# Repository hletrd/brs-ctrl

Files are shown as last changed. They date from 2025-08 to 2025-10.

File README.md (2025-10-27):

# BEHAVIOR Robot Suite: Streamlining Real-World Whole-Body Manipulation for Everyday Household Activities

## This repository is a fork of the original [BEHAVIOR Robot Suite](https://github.com/behavior-robot-suite/brs-ctrl) repository.

* A 3D printer–friendly version of the JoyLo arms, featuring optimized 3D models for improved printability and easier assembly.

### Changes

* Merged `jcC.obj` and `jcSpace_33mm.obj` into a single `jcC.obj`.
* Adjusted the M2 nut pocket in `jcA.obj` to be tighter to ensure the fit of the nut.
* Added a slight draft and chamfer to the bottom of `jcB.obj` to make the holder easier to insert.
* Reduced the height to 2.0mm from the motor insertion area in `l2.obj`, `l2back.obj`, `l4.obj`, `l5.obj`, and `jcC.obj` so that the motor can be freely moved without the parts touching each other.
* Fixed mesh issues in `l3.obj`.
* Added an alignment key to `l2.obj` and `l2back.obj` to ensure precise alignment during assembly.
* Reduced the face thickness of `l4.obj` from motor mounting side to prevent interference with `l5.obj`.
* Rotated all parts so they can be printed with the fewest possible supports.

#### Note

* The final dimensions of the JoyLo arms remain unchanged, except for the wrist hinge (if a spacer is inserted).
* If exact dimensions are critical, **do not insert the spacer**.
  * Note that the wrist hinge might damage the cable.

### Printing instructions

* Print all parts, one set per arm.
  * Mirror `jcA.obj` and `jcC.obj` for the right side.

#### Recommended printing parameters

* Material: PLA
* Layer height: 0.2mm
* Outer wall thickness: 0.8mm
* Infill density: 50%
* Infill pattern: Grid or Gyroid
* Supports: Required.
* Do not rotate. Just print as provided.
* Units are in millimeters.

#### Recommended printer setup

* Tested with Bambu X1 Carbon (0.4mm hardened steel nozzle) using BambuStudio as the slicer.
* Filament: Bambu PLA Basic.
* Default 0.20mm Standard profile with the following modifications:
  * Ironing Type: Top surfaces
  * Bottom shell layers: 5
  * Sparse infill density: 50%
  * Sparse infill pattern: Gyroid
  * Enable Support: Yes

### Assembly instructions

* Follow the [Assembly Guide](https://behavior-robot-suite.github.io/docs/sections/joylo/step_by_step_assembly_guidance.html) from the original repository.
* BOM are as following table. (for both arms)

#### 3D Printed Parts

| Part | Source | Description | Count | Notes |
|---|---|---|---|---|
| [`mount.obj`](hardware/joylo/mount.obj) | 3D Print | Part from the original repository. | 2 | |
| [`mountback.obj`](hardware/joylo/mountback.obj) | 3D Print | Part from the original repository. | 2 | |
| [`jcA.obj`](hardware/joylo/jcA.obj) | 3D Print | Part from the original repository. | 1 | |
| `jcA.obj` (Mirrored) | 3D Print | Mirror for the right side. | 1 | |
| [`jcB.obj`](hardware/joylo/jcB.obj) | 3D Print | Part from the original repository. | 2 | |
| [`jcC.obj`](hardware/joylo/jcC.obj) | 3D Print | Part from the original repository. | 1 | |
| `jcC.obj` (Mirrored) | 3D Print | Mirror for the right side. | 1 | |
| [`l2.obj`](hardware/joylo/l2.obj) | 3D Print | Part from the original repository. | 2 | |
| [`l2back.obj`](hardware/joylo/l2back.obj) | 3D Print | Part from the original repository. | 2 | |
| [`l3.obj`](hardware/joylo/l3.obj) | 3D Print | Part from the original repository. | 2 | |
| [`l4.obj`](hardware/joylo/l4.obj) | 3D Print | Part from the original repository. | 2 | |
| [`l5.obj`](hardware/joylo/l5.obj) | 3D Print | Part from the original repository. | 2 | |
| [`u2d2_mount.obj`](hardware/joylo/u2d2_mount.obj)| 3D Print | Part from the original repository. | 1 | |
| [`spacer.obj`](hardware/joylo/spacer.obj) |3D Print| Optional spacer for the wrist hinge. | 2 | If the wrist hinge is too tight, insert this spacer for easier assembly. |

#### Miscellaneous Parts

| Part | Description | Count | Notes |
|---|---|---|---|
| M2 x 12mm bolts | For securing `jcA.obj` to `jcC.obj`. | 4 | |
| M2 nuts | Used with M2 x 12mm bolts to secure `jcA.obj` to `jcC.obj`. | 4 | |
| M2 x 8mm screws | For mounting all motors on their housings. | 24 | |
| M2 x 6mm bolts | For mounting all motors onto rotational axes. | 64 | |
| M2 x 10mm screws | For mounting motors to the wrist hinge. | 4 | |
| M3 x 6mm nylon support (M) | For mounting the u2d2 board. | 4 | |
| M3 nuts | Used with M3 x 6mm nylon support (M) to mount the u2d2 board. | 4 | |

* Note the difference of bolts and screws.

---

<div align="center">

[Yunfan Jiang](https://yunfanj.com/),
[Ruohan Zhang](https://ai.stanford.edu/~zharu/),
[Josiah Wong](https://jdw.ong/),
[Chen Wang](https://www.chenwangjeremy.net/),
[Yanjie Ze](https://yanjieze.com/),
[Hang Yin](https://hang-yin.github.io/),
[Cem Gokmen](https://www.cemgokmen.com/),
[Shuran Song](https://shurans.github.io/),
[Jiajun Wu](https://jiajunwu.com/),
[Li Fei-Fei](https://profiles.stanford.edu/fei-fei-li)



**Conference on Robot Learning (CoRL) 2025**

[[Website]](https://behavior-robot-suite.github.io/)
[[arXiv]](https://arxiv.org/abs/2503.05652)
[[PDF]](https://behavior-robot-suite.github.io/assets/pdf/brs_paper.pdf)
[[Doc]](https://behavior-robot-suite.github.io/docs/)
[[Algorithm Code]](https://github.com/behavior-robot-suite/brs-algo)
[[Assembly Guide]](https://behavior-robot-suite.github.io/docs/sections/joylo/step_by_step_assembly_guidance.html)


[](https://behavior-robot-suite.github.io/docs/)



______________________________________________________________________
</div>

We introduce the **BEHAVIOR Robot Suite** (BRS), a comprehensive framework for learning whole-body manipulation to tackle diverse real-world household tasks. BRS addresses both hardware and learning challenges through two key innovations: **JoyLo** and [WB-VIMA](https://github.com/behavior-robot-suite/brs-algo).

JoyLo provides a general, cost-effective approach to whole-body teleoperation by integrating multifunctional joystick controllers mounted on the ends of two 3D-printed arms.  The mounting arms serve as scaled-down kinematic twins of the robot’s arms, enabling precise bilateral teleoperation. JoyLo also inherits key advantages of puppeteering devices, including intuitive operation, reduced singularities, and enhanced stability. By grasping the JoyCon controllers attached to the kinematic-twin arms, users can operate the arms, grippers, torso, and mobile base in unison. This significantly accelerates data collection by allowing users to perform bimanual coordination tasks, navigate safely and accurately, and guide the end-effectors to effectively reach various locations in 3D space.



## Getting Started

> [!TIP]
> 🚀 Check out the [doc](https://behavior-robot-suite.github.io/docs/sections/brs_ctrl/overview.html) for detailed installation and usage instructions!

To control the Galaxea R1 robot, simply do

```Python
from brs_ctrl.robot_interface import R1Interface
from brs_ctrl.robot_interface.grippers import GalaxeaR1Gripper

# Initialize the robot interface with grippers
robot = R1Interface(
    left_gripper=GalaxeaR1Gripper(
        left_or_right="left",
        gripper_close_stroke=0.0,
        gripper_open_stroke=100.0,
    ),
    right_gripper=GalaxeaR1Gripper(
        left_or_right="right",
        gripper_close_stroke=0.0,
        gripper_open_stroke=100.0,
    ),
)

# Control the robot
robot.control(
    arm_cmd={
        "left": left_arm_action,  # np (6,)
        "right": right_arm_action,  # np (6,)
    },
    gripper_cmd={
        "left": left_gripper_action,  # float between 0.0 and 1.0
        "right": right_gripper_action,  # float between 0.0 and 1.0
    },
    torso_cmd=torso_action,  # np (4,)
    base_cmd=mobile_base_action,  # np (3,)
)
```

To run real-robot JoyLo control, simply run

```bash
python3 scripts/joylo/real_joylo.py
```

To run data collection, simply run

```bash
python3 scripts/data_collection/start_data_collection.py
```

## Check out Our Paper
Our paper is posted on [arXiv](https://arxiv.org/abs/2503.05652). If you find our work useful, please consider citing us!

```bibtex
@inproceedings{
jiang2025brs,
title={{BEHAVIOR} Robot Suite: Streamlining Real-World Whole-Body Manipulation for Everyday Household Activities},
author={Yunfan Jiang and Ruohan Zhang and Josiah Wong and Chen Wang and Yanjie Ze and Hang Yin and Cem Gokmen and Shuran Song and Jiajun Wu and Li Fei-Fei},
booktitle={9th Annual Conference on Robot Learning},
year={2025},
url={https://openreview.net/forum?id=v2KevjWScT}
}
```

## License
This codebase is released under the [MIT License](LICENSE).

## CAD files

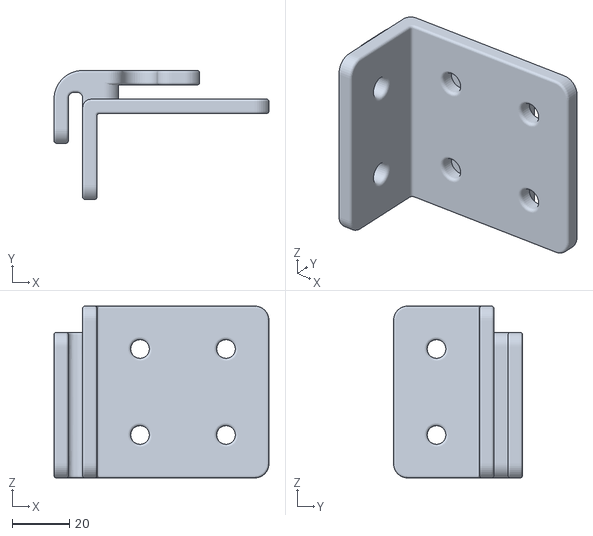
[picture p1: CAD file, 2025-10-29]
hardware/joylo/adapter.stl
75.0 x 45.0 x 60.0

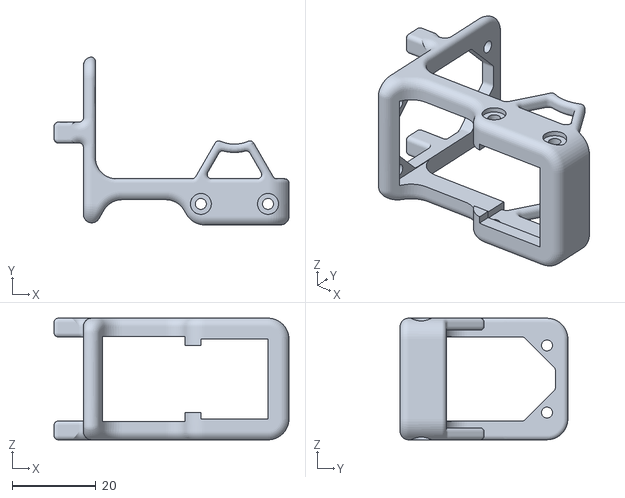
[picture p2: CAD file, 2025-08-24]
hardware/joylo_v2_7dof_arm/l7.obj
56.0 x 40.0 x 29.0

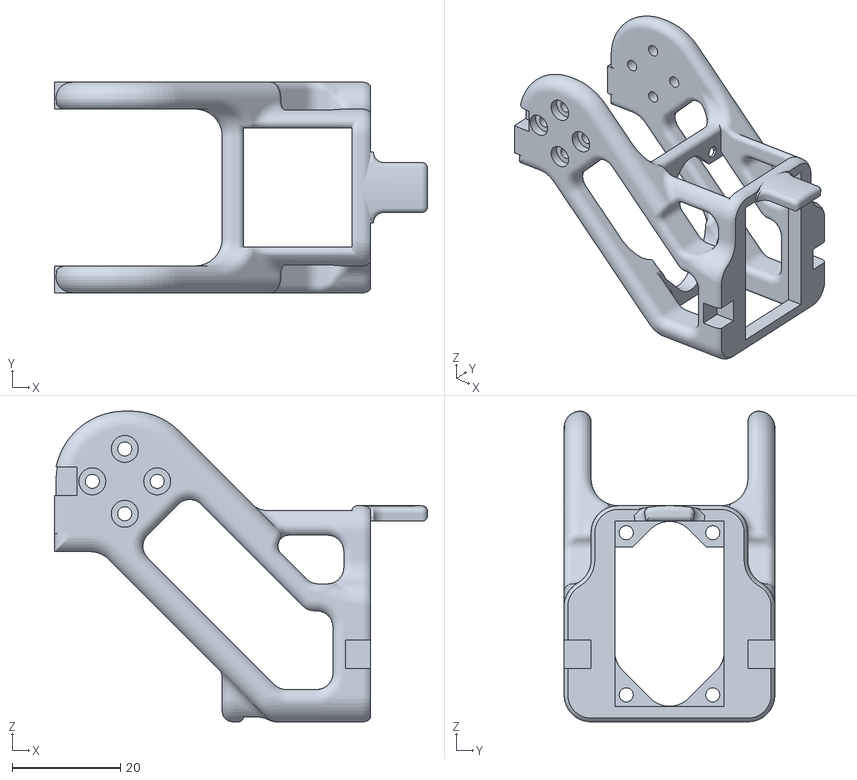
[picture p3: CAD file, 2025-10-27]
hardware/joylo/l4.stl
69.0 x 39.0 x 57.5

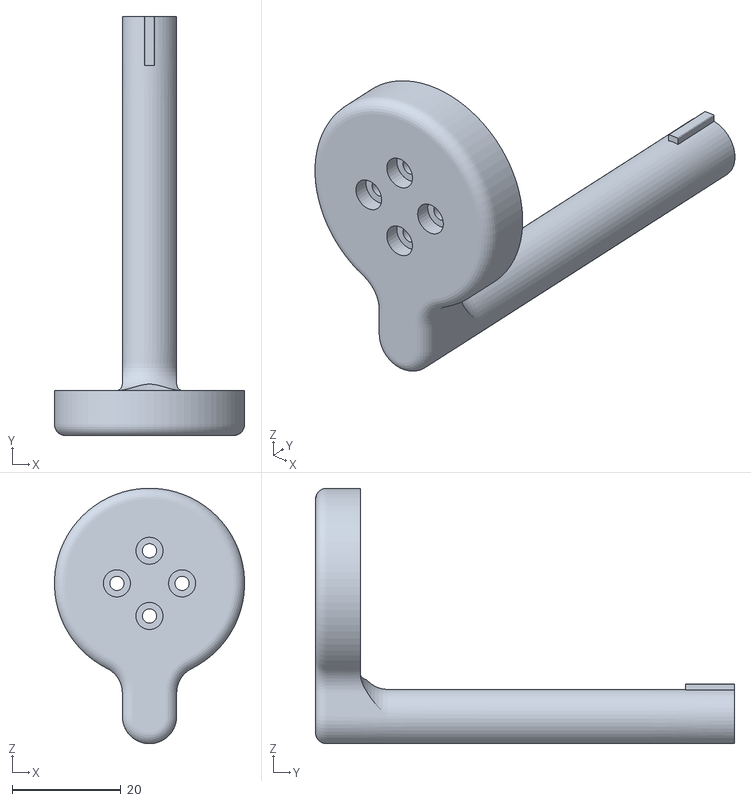
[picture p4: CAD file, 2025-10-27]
hardware/joylo/l2back.stl
35.0 x 77.1 x 47.0

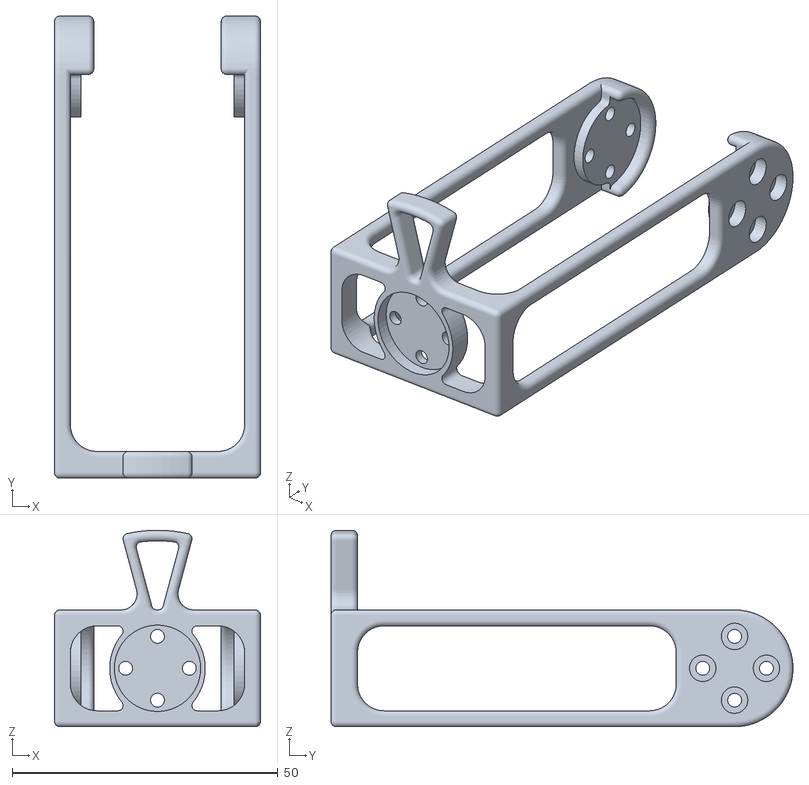
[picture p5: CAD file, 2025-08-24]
hardware/joylo_v2_7dof_arm/l6.obj
38.8 x 87.0 x 37.0

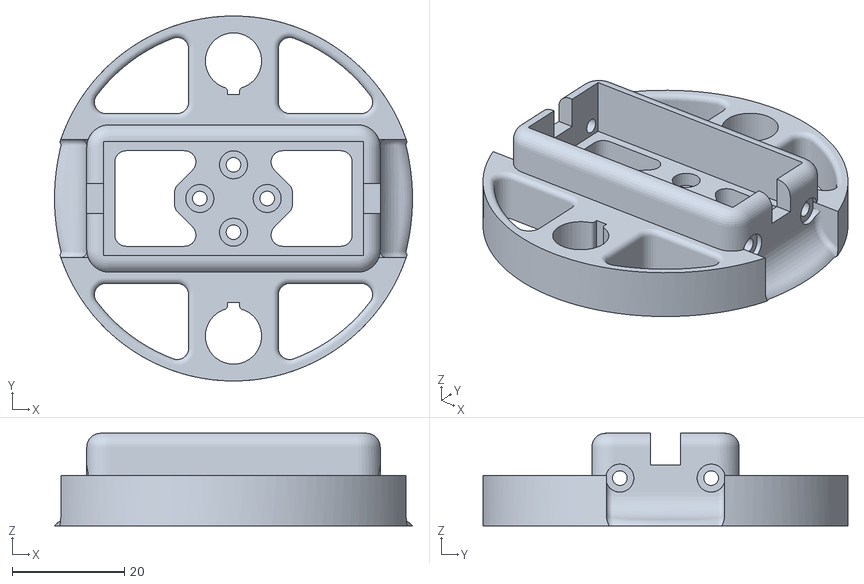
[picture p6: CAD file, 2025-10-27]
hardware/joylo/l2.stl
63.7 x 65.0 x 16.5

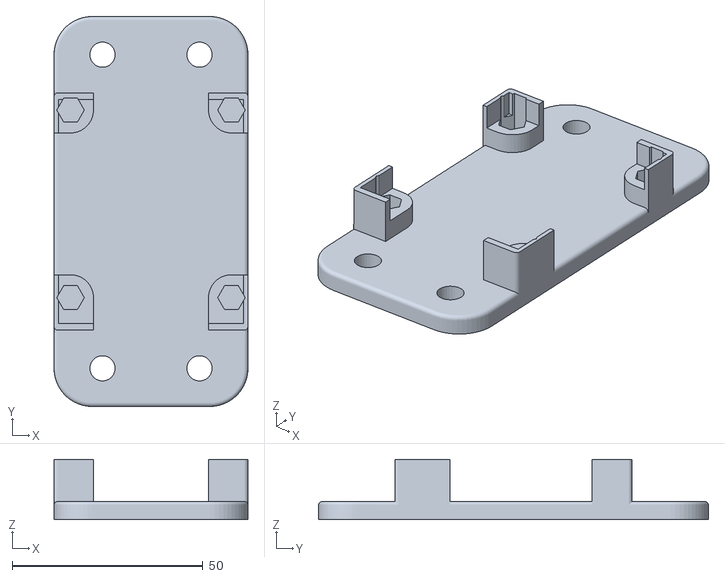
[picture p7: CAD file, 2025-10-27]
hardware/joylo/u2d2_mount.stl
50.8 x 102.1 x 15.8

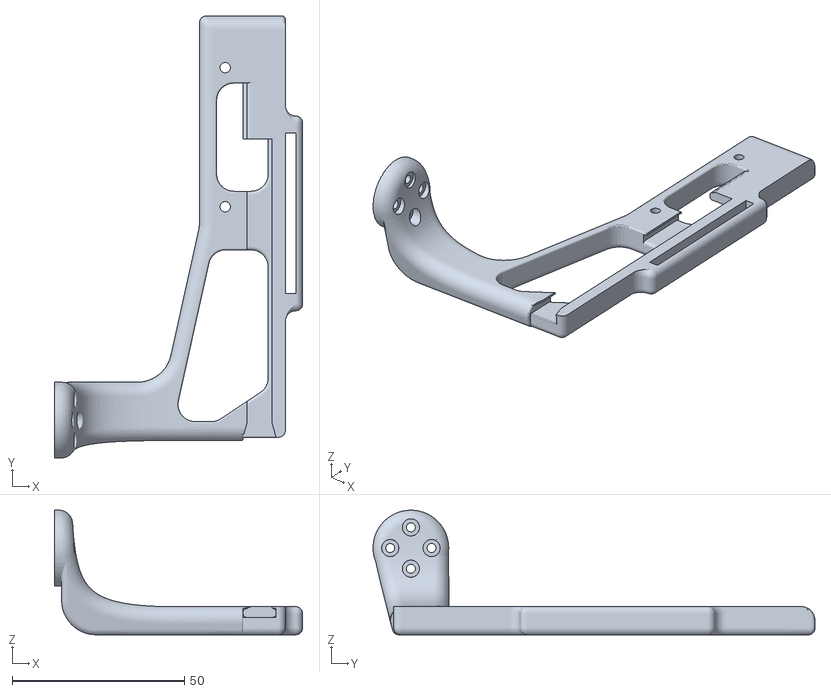
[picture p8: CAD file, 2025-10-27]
hardware/joylo/jcC.stl
72.1 x 128.3 x 36.2

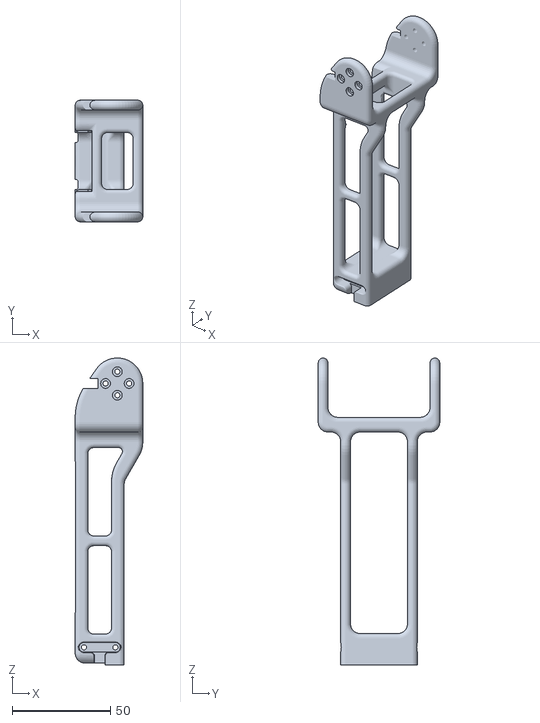
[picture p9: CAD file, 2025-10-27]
hardware/joylo/l3.stl
34.5 x 62.0 x 156.5

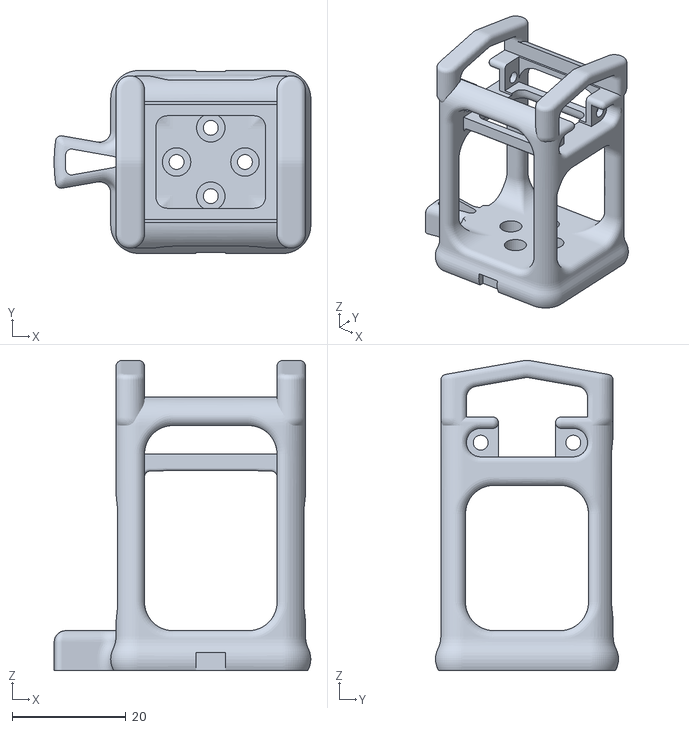
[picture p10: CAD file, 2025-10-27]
hardware/joylo/l5.stl
45.1 x 32.1 x 54.4

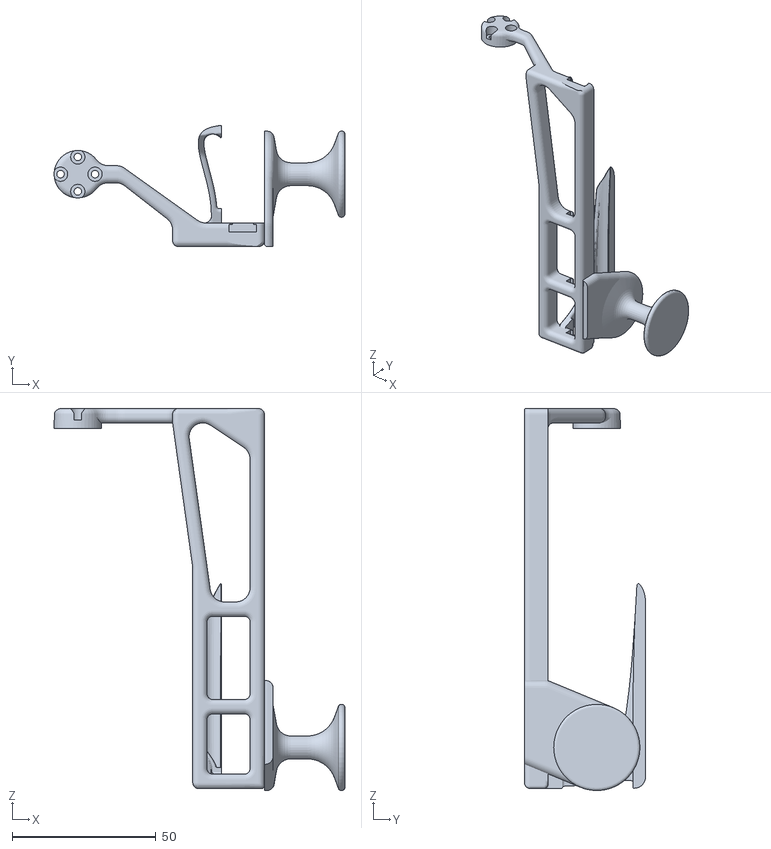
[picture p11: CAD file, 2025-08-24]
hardware/joylo_v2_7dof_arm/ljc.obj
101.2 x 42.2 x 133.0

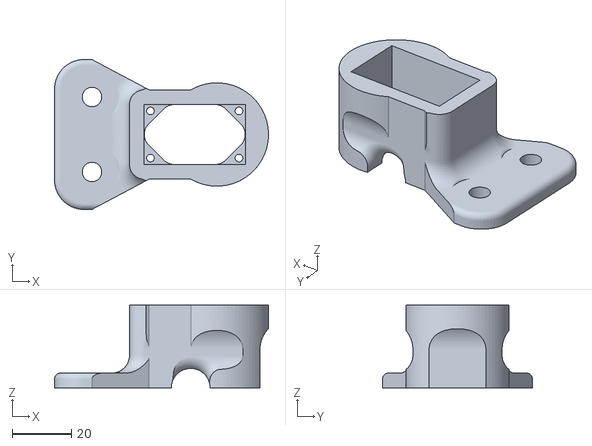
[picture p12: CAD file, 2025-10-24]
hardware/joylo/mount.stl
72.5 x 50.8 x 28.0

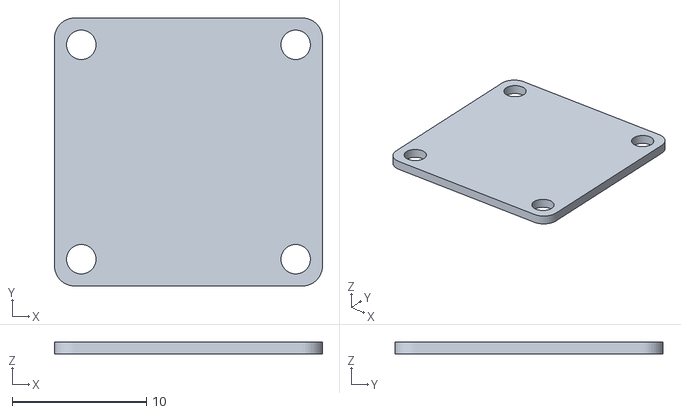
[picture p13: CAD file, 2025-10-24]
hardware/joylo/spacer.stl
20.0 x 20.0 x 0.9

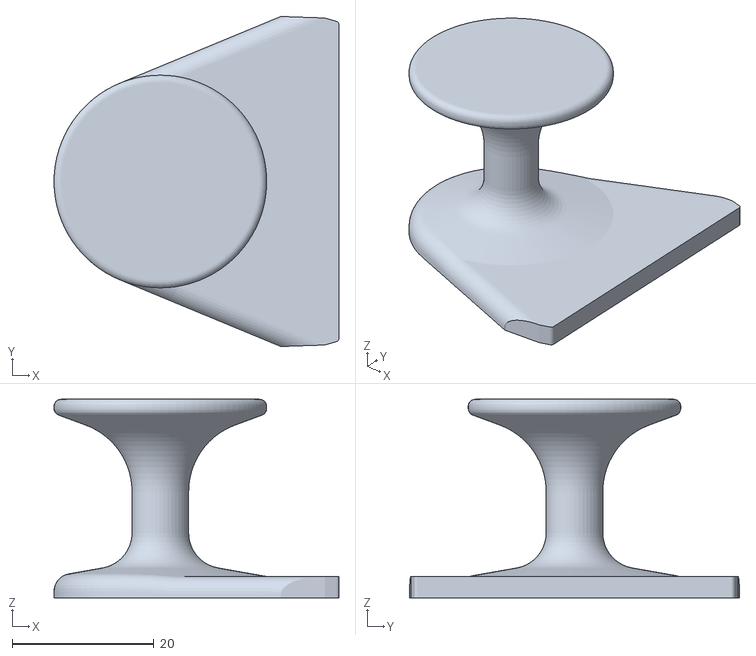
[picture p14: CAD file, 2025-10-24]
hardware/joylo/jcB.stl
40.2 x 46.6 x 28.0

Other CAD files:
hardware/joylo/jcA.stl
hardware/joylo/mountback.stl
hardware/joylo_v2_7dof_arm/l3.obj
hardware/joylo_v2_7dof_arm/l5.obj
hardware/joylo/adapter.obj
hardware/joylo/jcA.obj
hardware/joylo/jcB.obj
hardware/joylo/jcC.obj
hardware/joylo/l2.obj
hardware/joylo/l2back.obj
hardware/joylo/l3.obj
hardware/joylo/l4.obj
hardware/joylo/l5.obj
hardware/joylo/mount.obj
hardware/joylo/mountback.obj
hardware/joylo/spacer.obj
hardware/joylo/u2d2_mount.obj
hardware/joylo_v2_7dof_arm/l2.obj
hardware/joylo_v2_7dof_arm/l2back.obj
hardware/joylo_v2_7dof_arm/l4.obj
hardware/joylo_v2_7dof_arm/mount.obj
hardware/joylo_v2_7dof_arm/mountback.obj
hardware/joylo_v2_7dof_arm/u2d2_mount.obj

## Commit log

2025-08-24 add f3d files
    [jc.f3d, l2.f3d, l2back.f3d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]
2025-08-24 add 7dof joylo
    [l2.obj, l2back.obj, l3.obj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]
2025-10-24 updated mesh files
    [jcA.obj, jcA.stl, jcB.obj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]
2025-10-24 apply rotations
    [jcA.obj, jcA.stl, jcB.obj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]
2025-10-24 remove f3d files
    [jc.f3d, l2.f3d, l2back.f3d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]
2025-10-27 fix models
    [jcB.obj, jcC.obj, jcC.stl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]
2025-10-29 add extrusion adapter
    [adapter.obj, adapter.stl]
